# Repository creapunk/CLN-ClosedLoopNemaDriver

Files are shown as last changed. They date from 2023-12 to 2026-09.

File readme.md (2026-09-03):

# CLN - CLOSED-LOOP DRIVERS FOR NEMA MOTORS

    

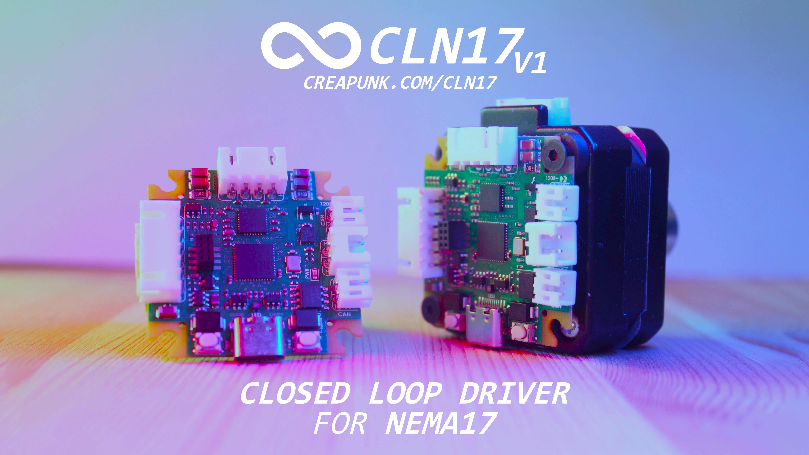
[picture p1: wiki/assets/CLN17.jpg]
CLN17 (https://www.youtube.com/watch?v=A67UROq0t6Q)


The CLN motor driver series is an **open-source** project aimed at creating a range of compact, cost-efficient high-performance closed-loop stepper drivers for various NEMA form factor motors. These drivers are designed to provide silent and smooth motion, high-precision position control, and energy-saving capabilities, suitable for a wide array of applications in robotics, CNC machines, 3D printers, and more.

## Key Features

- 🕹️ **Closed-Loop Control:** Integrates an encoder for real-time position monitoring, ensuring precise and safe motion.
- 📏 **Fine Positioning:** Achieves high position control accuracy of 0.01° for smooth operation.
- 🛡️ **Reliable Operation and Enhanced Safety:** Features integrated diagnostic and protection mechanisms for the motor and the user safety.
- 🧩 **Modular Concept:** Offers various configurations for different cost, size and performance needs, supporting expansion boards and daisy chain connections.

## Applications

- 🎓 Learning Platforms
- 🛠️ CNC Machines & 3D printers
- 🤖 Robotics & Automation Systems
- 🤝 Collaborative Robots
- 🔭 Camera & Telescope Stabilization Systems
- 🔬 Laboratory Equipment
- 🏭 Industrial Motion Control Systems
- 📳 Haptics & Force Feedback Systems

## Repository Structure

- **[`wiki`](wiki)**: includes design documentation and other information
- **[`hardware`](hardware)**: contains design source files, manufacturing files, schematics, block diagrams and 3D models

## Firmware

The following options are available:

- **[CLN-SimpleFOC](https://github.com/AntonEvmenenko/CLN-SimpleFOC):** SimpleFOC based firmware for CLN. Pretty stable, ready to use
- **[TunePulse](https://github.com/creapunk/TunePulse):** Firmware for CLN and RadiX motor drivers. Currently a work in progress; estimated release date is to be determined

## Hardware Versions

#### [NEMA17 dedicated drivers](./wiki/CLN17/readme.md)

- **[`CLN17 V3.0`](hardware/CLN17/V3.0)** [active]: newest version with best performance and BLDC support [[wiki]](./wiki/CLN17/V3.0/specification.md). 
  
  > - **Key info:** Discrete MOSFET based, 6-48V 3.2A<sub>RMS</sub> 4.5A<sub>PEAK</sub>, up to 60W output power, 21bit position feedback, dual-sided SMD only assembly
  > - **Supported interfaces:** STEP-DIR-EN, USB, CAN-FD, USART, I2C, SPI, ABZ
  > - **Supported motors:** Stepper, 3phase BLDC/PMSM
  >
  > 

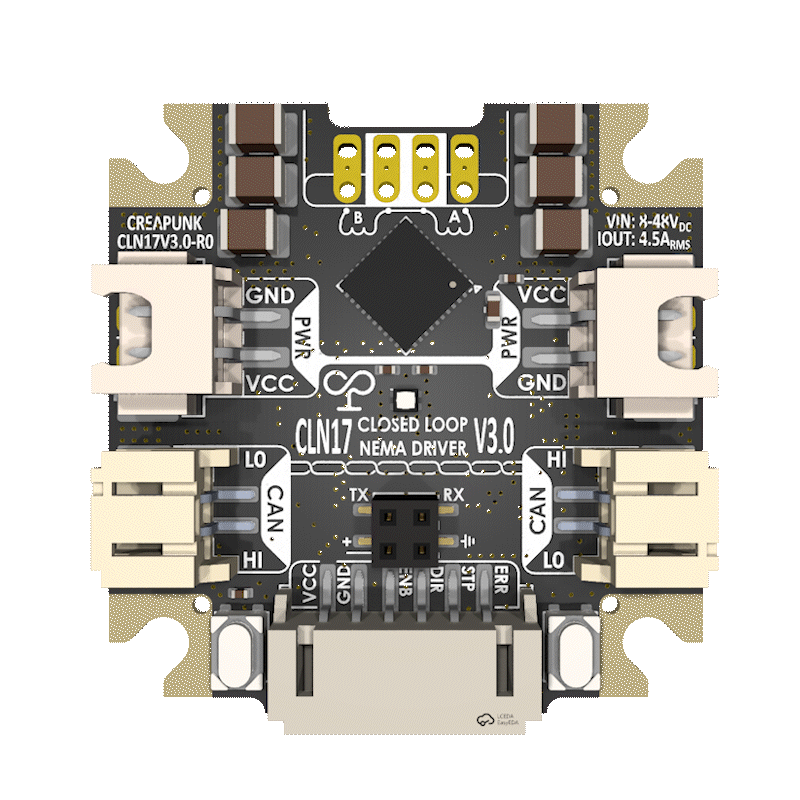
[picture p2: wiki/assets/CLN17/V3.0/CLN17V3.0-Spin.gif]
Preview
  

##### OBSOLETE / NRFND

**[`CLN17 V1.0`](hardware/CLN17/V1.0 [OBSOLETE])** [obsolete]: pilot version [[wiki]](./wiki/CLN17/V1.0/specification.md)

**[`CLN17 V1.5`](hardware/CLN17/V1.5 [OBSOLETE])** [tested]: cost-efficient version [[wiki]](./wiki/CLN17/V1.5/specification.md)

**[`CLN17 V2.0`](hardware/CLN17/V2.0 [NRFND])** [tested]: high voltage version [[wiki]](./wiki/CLN17/V2.0/specification.md). 
**[`CLN17 V2.1`](hardware/CLN17/ [NRFND])** is improved version

**[`CLN17 V2.5`](hardware/CLN17/V2.5 [NRFND])** [tested]: meant to be final version but will be skipped

***Important Note:** Obsolete designs will not be supported in future*

#### NEMA23 and NEMA34 dedicated drivers

- **[`CLN234 V1`](hardware/CLN234/V1.0)** [under tests]: powerful and versatile [[wiki]](./wiki/CLN234/V0.1/specification.md)

	> **Key info:** external MOSFETs, 8-75V 10A<sub>RMS</sub> 20A<sub>PEAK</sub>, up to 1000W output power, 21bit position feedback, 56x38x18mm, fits into Ø60mm
	>
	> **Supported interfaces:** STEP-DIR-EN, USB, CAN-FD, USART, I2C, SPI, ABZ
	
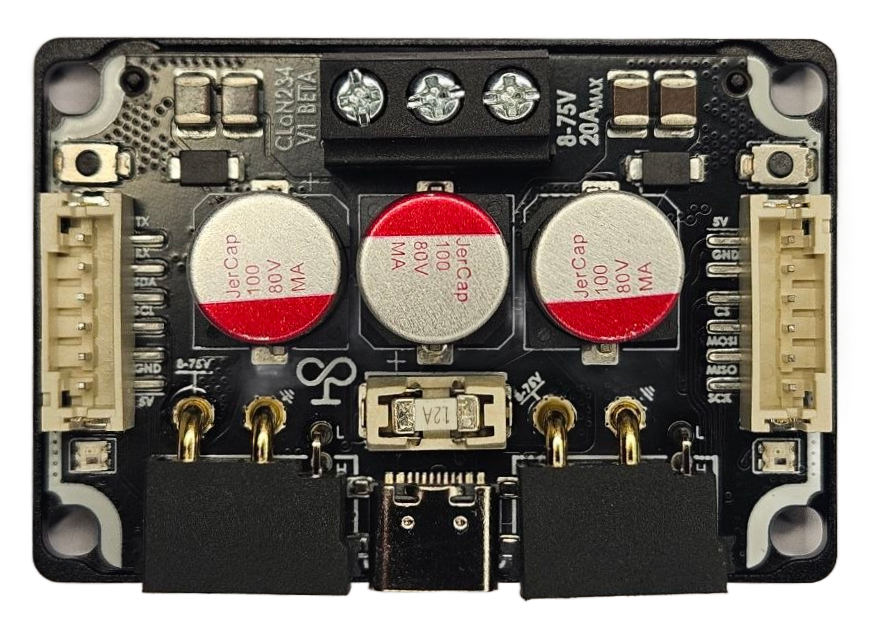
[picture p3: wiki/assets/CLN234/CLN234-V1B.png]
	

#### Modular drivers dedicated for embedded systems

Jump to the [RadiX project repository](https://github.com/creapunk/RadiX)

## Supporting the Project

If this project resonates with you, please consider the following ways to support its development:

- **[Ko-fi](https://ko-fi.com/creapunk):** Preferred for membership subscription and one-time donation
- **[Patreon](https://patreon.com/creapunk):** Alternative platform with higher fees
- **Join [Discord community](https://discord.gg/V4aJdTja8v):** Stay updated, engage in discussions, and contribute to the project

**Your contribution, regardless of size, is greatly appreciated!** 

*A heartfelt thank you to [everyone who supports this project](sponsors.md)!*

---

***Important Note:** This README will be updated to reflect the latest progress and changes in the project*.

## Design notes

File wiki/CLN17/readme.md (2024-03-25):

# CLN17 drivers series

| | CLN17 V2.0 | CLN17 V1.5 | CLN17 V1.0 |
| :---: | :---: | :---: | :---: |
| **MCU** | STM32G431CB<br/>M4 170MHz | STM32G431CB<br/>M4 170MHz | STM32G431CB<br/>M4 170MHz |
| **Memory** | 128KB FLASH<br/> 32KB SRAM | 128KB FLASH<br/> 32KB SRAM | 128KB FLASH<br/> 32KB SRAM |
| **Encoder** | TLE5012B<br/>15bit | TLE5012B<br/>15bit | TLE5012B<br/>15bit |
| **Driver** | DRV8844 | TMC2209 | TMC2209 |
| **Output power** | 8-48V<br/>1.75A<sub>RMS</sub> | 5-25V<br/>1.4A<sub>RMS</sub> | 5-25V<br/>1.4A<sub>RMS</sub> |
| **Max PWM frequency** | 75kHz | 40kHz | 40kHz |
| **Phase channel resistance** | 630mΩ | 270mΩ | 270mΩ |
| **Interfaces** | STEP-DIR<br/>USB2.0<br/>CAN-Bus FD<br/>USART<br/>I2C<br/>SPI / SSI<br/>ABZ | STEP-DIR<br/>USB2.0<br/>CAN-Bus FD<br/>USART<br/>I2C<br/>SPI / SSI<br/>ABZ | STEP-DIR<br/>USB2.0<br/>CAN-Bus FD<br/>UART<br/>I2C |
| **Size (WDH)** | 40x40x10mm | 40x40x10mm | 40x40x10mm |
| **Status** | Under testing | Tested | Obsolete |

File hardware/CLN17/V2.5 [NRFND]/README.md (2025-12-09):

- # CLN17 V2.5 Notes

	> #### Attention!
	>
	> This board has been tested, and the functionality of its main components has been confirmed. However, the board has several issues.
	>
	> You can proceed with its production, but it's recommended to wait for the updated V3 version. By using these files, you acknowledge and understand that:
	>
	> - This version is released for preview purposes only and may not receive future support.
	> - Any use of this version is at your own risk. The author is not responsible for any damage caused by the malfunction of this driver version.
	> - Subsequent versions may have changes in the BoM and the layout of all board components, including connectors.

	#### Known hardware issues:

	- Shorting VMOT when USB is plugged may cause unreversible damage of DCDC
	- Motor freewheeling when unpowered feature not work because of driver chip architecture
	- Current sensing may not work pr

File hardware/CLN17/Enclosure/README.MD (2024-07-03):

# Enclosure Design

> The enclosure design is compatible with all CLN17 drivers of versions V1.5, V2.0, [V2.5 future development].

### Stack

The enclosure consists of two halves: the **base plate**, which faces the motor, and the **cover**.

The **base plate** is responsible for positioning the board relative to the motor shaft and dissipating heat from the driver chip. The **cover** positions and secures the board within the **base plate** and protects the board from dust and mechanical damage.

A silicone thermal pad should be placed between the board and the **base plate**, specifically under the driver chip area.

The **cover** and **base plate** clamp the board between them using two DIN7991 M3x8mm screws located in two diametrically opposed threaded holes.

### Thermal Design

The most efficient heat dissipation from the driver chip is achieved through the copper and thermal vias in the board, rather than direct contact with the enclosure (due to R<sub>θJB</sub> Junction-to-board thermal resistance **<** R<sub>θJC(top)</sub> Junction-to-case thermal resistance).

Therefore, heat is conducted from the driver through PCB to the aluminum base plate via a silicone thermal pad.

The heat is then effectively distributed throughout the base plate due to its substantial thickness (2.5mm), reducing the temperature right under the driver chip.

Owing to the large thermal contact area between the base plate and the motor, the heat is evenly distributed between the motor and the base plate.

As a result, the driver can operate in an enhanced mode for an extended period without critical overheating, thanks to the motor's high thermal capacity.

Additionally, the built-in temperature sensor in the microcontroller allows for quick temperature readings (settling time <10s) of the aluminum plate (and consequently the motor), which further allows to optimize heat dissipation through algorithms.

### Enclosure Manufacturing

To manufacture the enclosure, two parts are required:

One `BASE-ALUMINUM.STEP` and one of [`COVER-POLYMER.STEP` or `COVER-POLYMER-TRANSPARENT.STEP` or `COVER-ALUMINUM.STEP`]. The choice is up to you.

Polymer parts can be made using any 3D printing process, though SLA is recommended.

For aluminum parts, the following requirements must be met to achieve best result:

- **Material:** Aluminum Alloys 6061, 5083, or 7075.
- **Minimum milling volume:** 45x45mm, with a thickness up to 10mm.
- **Milling Technology:** 3-axis milling on both sides.
- **Minimum tolerances and end mill diameter:** XY tolerance ±0.1mm, Z tolerance ±0.05mm, end mill diameter ≤ 2.0mm.
- **Postprocessing:** **Threading** of 2xM3 threads to a depth of 3mm, **chamfering**.
- **Surface finish:** Abrasive blasting, **anodizing** (preferably black).

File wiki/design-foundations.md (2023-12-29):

# Design Foundations

In any project, the philosophy and design concepts have a significant impact on its vision and purpose, extending beyond basic functionality. Incorporating design principles into the project can result in a solution that not only fulfills technical requirements but also resonates with users on an aesthetic level.

## Design philosophy

- 📖 **Open Source and Comprehensive Documentation:** Adopting an open-source philosophy invites wide-ranging engagement, making the project versatile and adaptable. Community involvement fosters innovation and knowledge exchange, creating a supportive ecosystem. Clear documentation promotes learning, collaboration, and seamless integration with other projects.
- 💎 **Aesthetic Appeal and Usability:** A technical product's aesthetic appeal should be a byproduct of its superior functionality, technological advancement, and usability.
- 💰 **Cost-Effectiveness and Accessibility:** Balancing cost and functionality while prioritizing accessibility ensures the project's seamless integration across various sectors.
- 🚀 **Future-Proofing:** Incorporating foresight for future improvements while maintaining the core design's integrity streamlines the development of new products. Proactively addressing and accommodating future requirements ensures the project's enduring viability and relevance.

## Design concepts

- 💪**High Performance:** The system should be capable of processing feedback data in real-time and react immediately by controlling the motor based on predefined algorithms. This simplifies the control process and reduces the load on the control device.
- 💻 **Compatibility and Versatility:** A wide range of supported interfaces should enable interaction with existing protocols as well as the implementation of new ones. This expands compatibility and facilitates integration of the device into existing systems.
- 🛡️ **Precision and Fault Tolerance:** The implementation of feedback control with position and current sensors should ensure precise positioning and mechanical load monitoring. This enables the detection and prevention of abnormal system operation when necessary.
- 🔧 **Adaptability:** Evaluating motor operating parameters and system displacement data enables the selection of an optimal motor control profile for the specified task.
- ⚡️ **Reliability and Power Efficiency:** Providing protection against electrostatic discharge (ESD), short circuits, and reverse polarity, as well as preventing overheating through reduced thermal losses, improved heat dissipation, and enhanced energy efficiency.
- 🧩 **Customizability and Modularity:** The device should accommodate functionality expansion or reduction without necessitating design changes.
- 🏭 **Optimized for Design for Manufacturing (DFM):** Complying with manufacturing technology requirements enhances manufacturability while reducing production costs and complexities.
- ⏳ **Longevity Considerations:** When choosing project component composition, future availability and support forecasts should be considered.

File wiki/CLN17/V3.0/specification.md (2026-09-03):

# CLN17-V3.0 Specification

## ⚡ Electrical characteristics

- **Input voltage:** 8-48VDC with overcurrent protection, reverse polarity protection and surge protection
- **Current requirements:** 3.2A<sub>RMS</sub> with up to 4.5A peak current
- **Powering options:**
	- 2-Pin connector **XH2.5** (3A limited by connector)
	- 6-Pin connector PH2.0 (2A limited by connector)
- **System voltage source:** 
	- On-board DC-DC converter
	- USB Type-C connector (5VDC 1.5A limited by design)

------

## 🔄 Motor Driving Control Capabilities

- **Best stepper motor form factor:** NEMA17
- **Maximum coil current:**
	- **3.0A<sub>RMS</sub>** per phase continuously
	- **4.5A<sub>PEAK</sub>** per phase continuously with heatsink
- **Maximum output voltage:** 48VDC
- **Maximum step sub-division resolution:** 1/256 of full step
- **Energy saving features:** Passive Braking, Freewheeling and automatic power down
- **Working frequency:** up to 83kHz PWM
- **Phase channel resistance:** MOSFETs RDS<sub>ON</sub> 45mΩ for both sides + 15mΩ current sensing resistor
- **True Driver positioning resolution:** Up to 0.028° (may be limited by motor)
- **True Encoder position feedback resolution:** 21bit per full rotation
- **Diagnostic functions:** overheat detection, short-circuit detection, under-voltage detection, open-load detection in case connectors are not firmly plugged in

------

## 🖥️ MCU Performance and External interfaces

**MCU:** High-performance Arm Cortex-M4 MCU **STM32G431CB** running at **170MHz** with:

* **128KB Flash** memory and **32KB SRAM** memory and **1Kb OTP**
* Math accelerator with trigonometric functions calculations support;
* True random number generator
* Internal HSI and RTC with external oscillator option

**Interfaces:**

* **USB2.0** for PC communication
* **CAN-Bus** with CAN-FD support for high-speed or long-range wired connection with daisy chain connection option

- **SWD** programming interface with debug over SWO trace
- **6-Pin CTRL connector PH2.0** with multifunctional bidirectional fast 4-Pin interface up to 8MHz with support:
  * **Classic EN/DIR/STEP** interface with **ERR line**

  * **USART** (Single wire, Asynchronous, Synchronous)

  * **I2C**

  * **SPI or SSI**

  * **ABZ incremental interface** for external encoder connection with program-controlled **5V voltage source**

  * **Custom interface** including numerous combination of the above interfaces
- **4-Pin expansion connector 2x2P2.0** with 2A power line and multifunctional bidirectional fast 2-Pin interface up to 8MHz with **Classic UART** interface

**I/O protection features**:

* ESD protection (persistent against electrostatic discharge)
* USB, SWD and control interfaces are 5V-tollerant
* Reverse polarity signal protection
* Overcurrent protection

**User interaction:**

*  **2** programmable custom **user buttons** (one can be used as reset button)
*  **RGB LED** for indication of working mode or current status

------

## 📏 Mechanical data

- **Size dimensions:** PCB outline is 40x40mm (adapted for NEMA17 form factor) 8.5-13mm total height (depends on the connectors type)
- **Driver housing:** 42x42mm CNC-milled alluminum case for PCB mounting, heatsink and mechanical protection with
- Weight: 
	- **10g**   board only
	- **20g** board with mount

------

## 🔥 Operating conditions

* **Working temperature range:** **-25 to +80** degrees Celsius
* **Environment humidity range:** 0 to 90%
* **Environmental safety:** potential **Lead-Free** and **RoHS** compliance
* **Maximum heat dissipation**: 3W from motor driver and 0.5W from other system

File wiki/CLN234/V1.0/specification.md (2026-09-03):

# CLN234-V1 Specification

## ⚡ Electrical characteristics

- **Input voltage:** 8-75VDC with overcurrent protection, reverse polarity protection and surge protection
- **Current requirements:** 10A<sub>RMS</sub> with up to 20A peak current
- **Powering options:**
	- XT30 2+2
- **System voltage source:** 
	- On-board DC-DC converter
	- USB Type-C connector (5VDC 1.5A limited by design)

------

## 🔄 Motor Driving Control Capabilities

- **Supported motor type:** Dual DC, Steppers, BLDC, PMSM
- **Supported NEMA motors:** NEMA23, NEM34, NEMA42, other
- **Maximum phase current:**
	- **10A<sub>RMS</sub>** per phase continuously
	- **13A<sub>RMS</sub>** per phase with 50% duty cycle (period 1s)
	- **20A** peak per phase
- **Maximum output voltage:** 75VDC
- **Maximum step sub-division resolution:** 1/512 of full step
- **Energy saving features:** Passive Braking, Freewheeling and automatic power down
- **Working frequency:** up to 83kHz PWM
- **Phase channel resistance:** Mosfets RDS<sub>ON</sub> 20mΩ for both sides + 2.5mΩ current sensing resistor
- **Encoder position feedback resolution:** 21bit per full rotation
- **Diagnostic functions:** overheat detection, short-circuit detection, under-voltage detection, open-load detection

------

## 🖥️ MCU Performance and External interfaces

**MCU:** High-performance Arm Cortex-M4 MCU **STM32G431CB** running at **170MHz** with:

* **128KB Flash** memory and **32KB SRAM** memory and **1Kb OTP**
* Math accelerator with trigonometric functions calculations support;
* True random number generator
* Internal HSI and RTC with external oscillator option

**Interfaces:**

* **USB2.0** for PC communication
* **CAN-Bus** with CAN-FD support for high-speed or long-range wired connection with daisy chain connection option

- **SWD** programming interface with debug over SWO trace
- First **5-Pin CTRL connector PH2.0**:
  * **Classic EN/DIR/STEP** interface with **ERR line**
  * **USART** (Single wire, Asynchronous, Synchronous)
  * **SPI or SSI**
  * **ABZ incremental interface** for external encoder connection with program-controlled **5V voltage source**
- Second **5-Pin CTRL connector PH2.0**:
	- **Classic EN/DIR/STEP** interface or **DIR/STEP** with **ERR line**
	- **I2C**
	- **ABZ incremental interface** for external encoder connection

- **4-Pin expansion connector 2x2P2.0** with 2A power line and multifunctional bidirectional fast 2-Pin interface up to 8MHz with **Classic UART** interface

**I/O protection features**:

* ESD protection (persistent against electrostatic discharge)
* USB, SWD and control interfaces are 5V-tollerant
* Reverse polarity signal protection
* Overcurrent protection

**User interaction:**

*  Reset button

------

## 📏 Mechanical data

- **Size dimensions:** 
	- PCB outline: 54x54mm (adapted for NEMA23 form factor)
	- PCB circumcircle radius: 60mm
	- PCBA Height: 15mm

- Weight: 
  - **8g**   board only
  - **18g** board with mount
  - **24g** with **low-profile** aluminum housing
  - **28g** with **full-size** aluminum housing

------

## 🔥 Operating conditions

* **Working temperature range:** **-25 to +80** degrees Celsius
* **Environment humidity range:** 0 to 90%
* **Environmental safety:** potential **Lead-Free** and **RoHS** compliance
* **Maximum heat dissipation**: 20W from motor driver and 0.5W from other system

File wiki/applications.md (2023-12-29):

# Applications

The CLN17 Stepper Motor Driver is suitable for a wide range of applications, including but not limited to the listed below.

## Learning and Research

- 🎓 **Learning Platforms:** Open-source designs and clear documentation provide universal motor control learning solutions, promoting innovation and collaboration among students and educators. <br/>*Examples: Robotic arm kits; Solar tracking systems.*
- 🔬 **Laboratory Equipment:** Precision, safety, and feedback features are crucial for reliable operation, accurate results and researcher safety. <br/>*Examples: Automated liquid handling systems; Precision sample positioning systems.*
- 🤝 **Cobots and Learning Systems:** Accurate shaft position and speed detection make the motor driver suitable for cobots and learning systems, enabling safe human-machine collaboration. <br/>*Examples: Humanoid robots for social interaction; Collaborative robotic arms for assembly tasks.*

## Robots and Automotion

- 🛠️ **CNC Machines & 3D Printers:** Precision and error-free positioning are essential for accurate manufacturing in CNC machines and 3D printers. <br/>*Examples: High-speed or large-format 3D printers; Laser cutting and engraving machines; Desktop CNC milling machines.*
- 🤖 **Robotics & Automation Systems:** Precise control and movement enhance overall performance in robotics and automation. <br/>*Examples: Autonomous mobile robots; Pick-and-place robotic systems.*
- 🏭 **Industrial Motion Control Systems:** Reliability and compatibility with industrial interfaces improve performance in industrial motion control.<br/>*Examples: Conveyor systems and Delta-Robots; Automated assembly lines.*

## Haptic and Stabilization

- 📳 **Haptics & Force Feedback Systems:** Accurate current and force control are vital for realistic haptic and force feedback experiences. <br/>*Examples: Teleoperation systems for remote control; Virtual reality controllers with force feedback.*
- 🔭 **Camera/Telescope Stabilization Systems:** Stable orientation in camera and telescope systems relies on precise positioning and position holding, simplifying system calibration for accurate component alignment. <br/>*Examples: Motorized telescope mounts; Video camera sliders.*

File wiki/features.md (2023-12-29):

# Features

## Position Control and Accuracy

- 🕹️ **Closed-Loop Control:** The motor driver supports closed-loop control, integrating an encoder for real-time position monitoring and adjustment, ensuring precise motion in challenging conditions.
- 📏 **Fine Positioning:** Exceptional position control accuracy of 0.01° ensures efficient and low latency processing of position information and minimal noise for smooth operation.
- 🎯 **Extremely Precise and Repeatable Sensorless Parking:** The sophisticated sensorless parking algorithm accurately positions the motor without additional sensors, preventing system damage.

## Performance and Efficiency

- 💪 **Adaptive Torque Control and Energy Efficiency:** The motor driver adjusts torque based on load requirements, optimizing energy efficiency, reducing stress, and extending motor lifespan.
- 🚀 **High Performance:** A 32-bit 170MHz ARM Cortex®-M4 microprocessor delivers significant performance improvements and ample power for application code.
- 🔇**Ultra-Silent and Smooth Operation:** The silent motor driver guarantees quiet and smooth operation for noise and vibration-sensitive applications.
- ⏩ **Passive braking and freewheeling:** Smooth deceleration and coasting of the motor are enabled by passive braking and freewheeling functionalities, enhancing control and efficiency.

## Compatibility and Modularity

- 🤝 **Open-Source Approach:** Complete access to hardware schematics, PCB layouts, firmware, and software fosters transparency, collaboration, and innovation, enabling the creation of customized solutions.
- 💻 **Enhanced compatibility:** Versatile connectivity options, including UART, I2C, CAN-Bus (with FD support), USB2.0 over Type-C and more, facilitate seamless communication and easy integration into existing systems.
- 🧩 **Modular Concept:** Various configurations meet size and performance requirements while maintaining cost-effectiveness, supporting expansion boards for additional functionalities.
- 🌐 **Efficient Daisy Chain Interconnection:** Enables direct connection of multiple drivers, simplifying setup and reducing the need for extra interfacing hardware.

## Safety and Reliability

- 🔧 **Robust and Reliable Performance:** Designed to operate reliably across a wide temperature range. Includes diagnostic functions and built-in protections against ESD, current limitation, reverse polarity, overload, and supports 3.3V/5V IO tolerance.
- 🛡️ **Intelligent Safety Algorithms:** Advanced algorithms continuously monitor motor conditions, providing proactive protection to both the motor system and users from potential harm.
- ⏰ **High-Precision Real-Time Clock:** Incorporates a precise clock source, essential for time-sensitive operations, ensuring accurate timing for critical tasks and reliable code execution.

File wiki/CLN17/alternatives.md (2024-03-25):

# Alternative Closed-Loop Drivers for NEMA17

CLN17 is not the only closed-loop motor driver. There are several alternatives available, which are also closed-loop drivers and designed with a similar architecture. These drivers comprise a microcontroller, an encoder, and a driver, all integrated onto a single printed circuit board placed at the rear side of the NEMA17 motor.

## Quick overview of the alternatives

- [USTEPPER S32](https://github.com/uStepper/uStepperS) by [uStepper](https://github.com/uStepper)
- [MKS SERVO42C](https://github.com/makerbase-mks/MKS-SERVO42C) by [Makerbase](https://github.com/makerbase-mks)
- [MECHADUINO](https://github.com/jcchurch13/Mechaduino-Hardware) by [jcchurch13](https://github.com/jcchurch13)
- [XDrive](https://github.com/unlir/XDrive) by [unlir](https://github.com/unlir)
- [BTT S42C](https://biqu.equipment/products/bigtreetech-s42c-v1-0-42-stepper-motor-closed-loop-driver-board-with-oled-display) by [BigTreeTech](https://github.com/bigtreetech)
- [Smart Stepper](https://github.com/Misfittech/nano_stepper) by [Misfittech](https://github.com/Misfittech)
- [Ethersweep](https://github.com/Neumi/ethersweep) by [Neumi](https://github.com/Neumi)

| | CLN17 V2 | USTEPPER S32 | MKS SERVO42C | BTT S42C | MECHADUINO | Smart Stepper | XDrive | Ethersweep |
| :---: | :---: | :---: | :---: | :---: | :---: | :---: | :---: | :---: |
| **MCU** | STM32G431CB<br/>M4 170MHz | STM32F401RE<br/>M4 84MHz | HC32L130F8<br/>M0 48MHz | STM32G031G8<br/>M0+ 64MHz | ATSAMD21G18<br/>M0+ 48MHz | STM32F103CB<br/>M3 72MHz | STM32F103CB<br/>M3 72MHz | STM32F103C8<br/>M3 72MHz |
| **Memory** | 128KB FLASH<br/> 32KB SRAM | 512K FLASH<br/>96K SRAM | 64KB FLASH<br/>8KB SRAM |  64KB FLASH<br/>8KB SRAM  | 256KB FLASH<br/>32KB SRAM | 256KB FLASH<br/>32KB SRAM | 128KB FLASH<br/>20KB SRAM | 64KB FLASH<br/>20KB SRAM |
| **Encoder** | TLE5012B<br/>15bit | TLE5012B<br/>15bit | MT6816<br/>14bit | TLE5012B<br/>15bit | AS5047D<br/>14bit | AS5047D<br/>14bit | MT6816<br/>14bit | AS5600<br/>12bit |
| **Driver** | DRV8844 | TMC5130 | EG3013<br/>CJ3400 | EG3013<br/>A03400 | A4954 | A4954 | TB67H450 | TMC2209 |
| **Output power** | 8-48V<br/>1.75A<sub>RMS</sub> | 8-42V<br/>1.4A<sub>RMS</sub> | 7-28V<br/>3.0A<sub>RMS</sub> | 12-24V<br/>3.0A<sub>RMS</sub> | 8-25V<br/>2.0A<sub>RMS</sub> | 8-35V<br/>2.0A<sub>RMS</sub> | 6-38V<br/>2.5A<sub>RMS</sub> | 6-30V<br/>1.4A<sub>RMS</sub> |
|  **Interfaces**  | STEP-DIR<br/>USB2.0<br/>CAN-Bus FD<br/>USART<br/>I2C<br/>SPI / SSI<br/>ABZ | STEP-DIR<br/>UART<br/>SPI<br/>I2C | STEP-DIR<br/>UART | STEP-DIR<br/>UART<br/>SPI | STEP-DIR<br/>USB2.0<br/>SPI<br/>I2C | STEP-DIR<br/>USB2.0<br/>UART<br/>I2C | STEP-DIR<br/>USB2.0 or CAN-Bus<br/>RS485 | USB2.0<br/>SPI<br/>I2C<br/>Ethernet |
|  **Size (WDH)**  | 40x40x10mm | 42x42x12mm | 43x40x12mm | 40x40x12mm | 42x42x16mm | 42x42x16mm | 40x40x12mm | 40x40x25mm |
| **Status** | Open-Source | Open-Source | Open-Source | Proprietary | Open-Source | Open-Source | Open-Source | Open-Source |

> The following information is sourced from the analysis of datasheets, official descriptions, and other reliable sources. However, please note that it may be outdated, inaccurate, or incomplete.

## Is there anything else?

There are several other similar products available, but they haven't been described due to the project's confidentiality or lack of information.

- [Emm42](https://github.com/Macrobase-tech/Emm42) by [Macrobase-tech](https://github.com/Macrobase-tech). Status: proprietary
- [AnanasStepper](https://github.com/AnanasRobot/AnanasStepper) by [AnanasRobot](https://github.com/AnanasRobot). Status: V3.0 not released
- [PANdrive](https://www.trinamic.com/products/pandrive-smart-motors/) by [Trinamic](https://www.trinamic.com/). Status: proprietary

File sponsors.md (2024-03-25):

# Project Contributors
A Heartfelt Thanks to Project Supporters and Contributors!

### Industry Supporters

Special thanks to [JLCPCB](https://jlcpcb.com/?from=creapunk) for their support with board manufacturing!

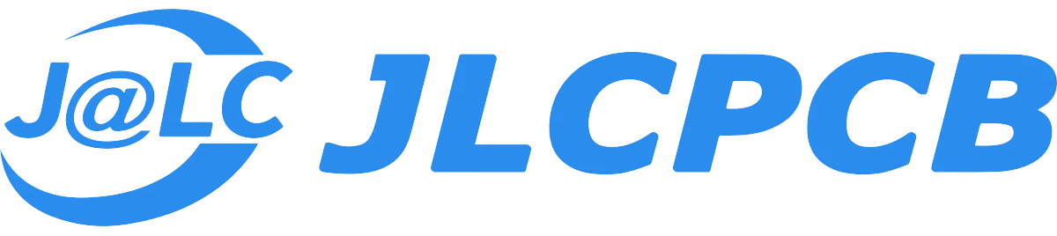
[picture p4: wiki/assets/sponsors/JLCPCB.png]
(https://jlcpcb.com/?from=creapunk)


## Community Sponsors

I'm grateful for the contributions from our community sponsors:

- Miral Patel

- @keverin16

- @olov

- @sharwin24

- @Denis2020

- @raghava

- @nathanjaker

- Henry Well

- Jeremy Fleming

- Robert Montini

- Vincent Wüthrich

Your support makes a significant difference in our project's progress. Thank you!

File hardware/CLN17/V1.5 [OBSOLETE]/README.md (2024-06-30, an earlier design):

#  CLN17 V1.5 HARDWARE



Compact driver for NEMA17, a corrected and improved version of CLN17 V1.0, suitable for 12V and 24V systems with a current of up to 1.4A RMS.

`STATUS` As of January 2024, the [board's functionality has been confirmed](#tested-hardware-features), with no problems identified. Firmware is in progress.

- [`Specification`](/wiki/CLN17/V1.5/specification.md)
- [`PCBA Manufacturing`](#pcba-manufacturing-specification)

------

### Board Diagram

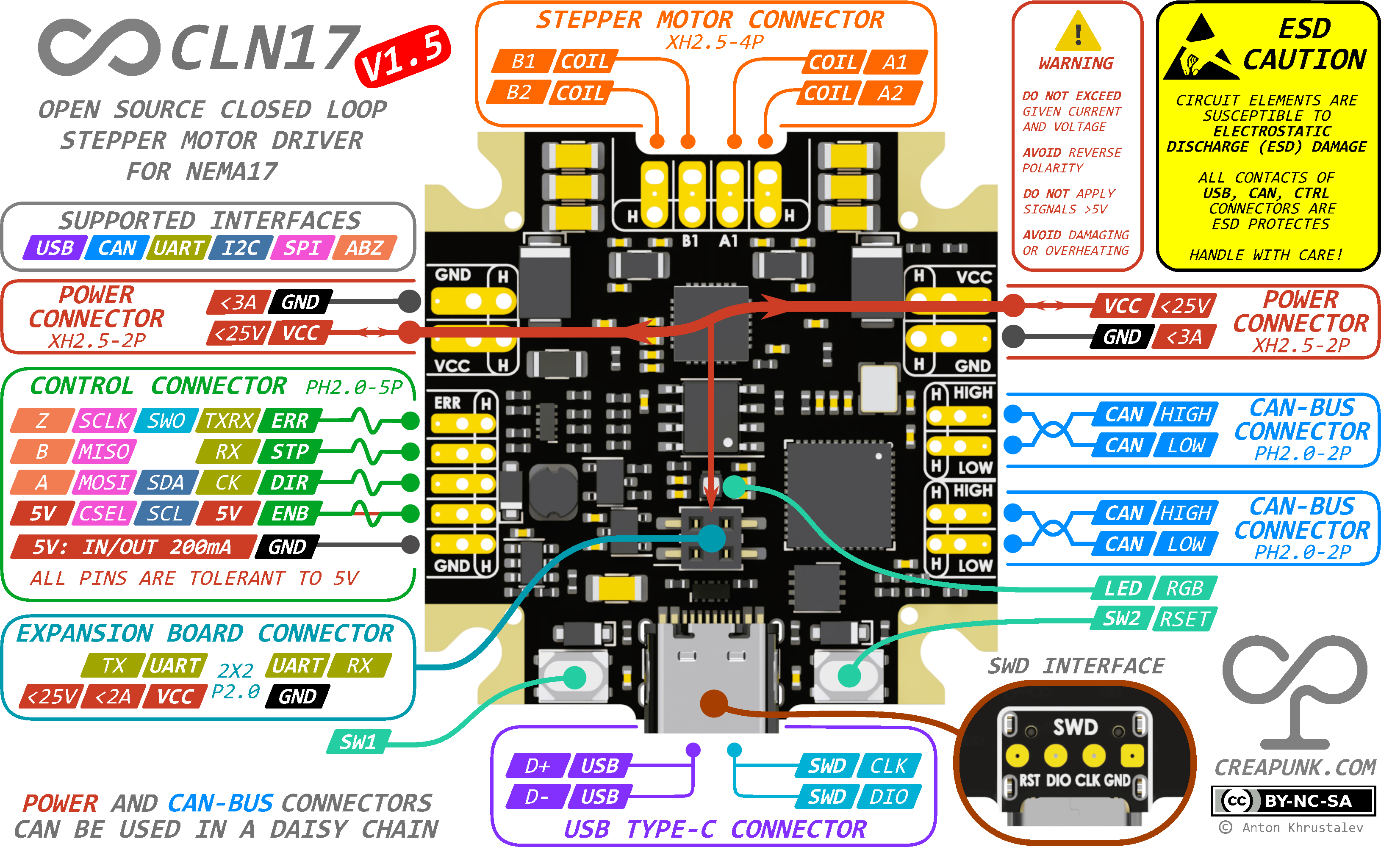
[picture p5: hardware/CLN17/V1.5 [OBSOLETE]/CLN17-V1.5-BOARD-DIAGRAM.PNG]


------

### Attention!

> - **Uncompleted firmware:** Firmware of CLN17 V1.5 driver is in active development. May contain unforeseen issues.
>
> - **Potential Design Changes:** The design may undergo minor modifications in the future.
>
> - **No Author Liability:** The author bears no responsibility for any damages resulting from incorrect usage, connections, manufacturing faults, or coding errors.
>
> - **User's Duty:** Users must conduct comprehensive tests in their specific environments. Adherence to provided usage guidelines is crucial.

------

### Tested hardware features

Driver IC:

- ✅ TMC2209 STEP-DIR, UART SW bidirectional communication, Reset + Disable functionality
- ✅ Freewheeling when unpowered
- ✅ Analog Current sensing

Encoder IC:

- ✅ TLE5012 SPI communication
- ✅ TLE5012 through the PCB position sensing (1LSB noise)

Power:

- ✅ Daisy Chain Power connection
- ✅ DCDC stability at voltage range [External: 5.2V-25V, USB: 4.9V-5.5V]
- ✅ ENB CLTR 5V (Power Sink & Source 5V 200mA)

Interfaces:

- ✅ USB communication
- ✅ CTRL connector - UART, I2C, SPI communication (ABZ not tested yet)
- ✅ CAN-Bus IC Shutdown and Logic supply, diff signal generation
- ✅ Expansion connector - UART communication
- ✅ SWD with reset functionality

Peripherals:

- ✅ SW1 & SW2 as button
- ✅ RESET using SW2 as output
- ✅ RGB LED (single color indication)
- ✅ External Precise Clock (10ppm) (HSE)

------

### PCBA Manufacturing Specification

- **Layers**: 4
- **Minimum Via Hole Size/Via Diameter**: 0.25mm/0.41mm
- **Minimum track width/spacing**: 0.13mm/0.13mm
- **Material**: FR4
- **PCB Thickness**: 1mm [preferred]
- **PCB Color**: Any, but black is more aesthetic.
- **PCB Surface Finish**: ENIG [preferred]
- **Outer/Inner Copper Weight**: 1oz/0.5oz
- **Via Covering**: Plugged [preferred] or Tented
- **Board Outline Tolerance**: ±0.2mm
- **Panelization**: optional, but if horizontal connectors used, the gap between boards should be ≥5mm.
- **Assembly**: Single top side
- **Tooling Holes**: Already present 4x D1.152mm in the corners of the board. May require modification for specific equipment.

#### Important Notes

> ***Non-stock Components Note:** The design features 3 irreplaceable components: the driver chip, microcontroller, and encoder. Other parts can be replaced with in-stock equivalents that match or surpass the original specs, provided you conduct a schematic review beforehand.*

> ***Cost Reduction Note:** Eliminate unused components such as the CAN-Bus or CTRL connector to reduce costs, provided you conduct a schematic review beforehand.*

------

### Support the Project!

**If you like the project and want to support its development, you can do so through:**

- **[Ko-fi](https://ko-fi.com/creapunk)** (*preferred for membership subscription and one-time donation*) - here, you can sign up for monthly support, or you can make a one-time donation as well!
- **[Patreon](http://patreon.com/creapunk)** - similar to Ko-fi, but with higher fees.

Don't forget to join **[creapunk community on Discord](https://discord.gg/4uFSsffhMt)** for the latest updates and discussions!

------

Special thanks to [JLCPCB](https://jlcpcb.com/?from=creapunk) for sponsoring the board manufacturing of this design!

(https://jlcpcb.com/?from=creapunk)

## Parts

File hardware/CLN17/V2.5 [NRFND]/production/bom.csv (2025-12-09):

Designator | Footprint | Quantity | Value | LCSC Part #
C1, C12, C13, C14, C5, C8, C9 | C1210 | 7 | 10u 100V | C5156756
C10 | C0402 | 1 | 2.2u | C12530
C11, C15, C29 | C0402 | 3 | 1u | C52923
C16, C2, C20, C35 | C0402 | 4 | 10u | C15525
C17, C18, C21, C22, C25, C26, C28, C3, C31, C4 | C0402 | 10 | 100n | C1525
C23 | C0603 | 1 | 22n 100V | C313083
C6, C7 | C0402 | 2 | 12p | C1547
D1 | D_SMAF | 1 | SMBJ48A | C353356
D3, D7 | D_SOD-123F | 2 | SS210 | C183475
D4 | D_SMAF | 1 | ES3BF | C437835
D6 | LED_RGB_0606 | 1 | LED_RABG | C2874115
FB1 | R0402 | 1 | <1R | C76883
IC1 | QFN-48-1EP_7x7mm_P0.5mm_EP5.6x5.6mm | 1 | STM32G431CB | C529356
J1, J2 | XH2.54 2P | 2 | PWR | C2908611
J3 | USB-TYPE-C-31-M-12 | 1 | TYPE-C-31-M-12 | C2988369
J4 | XH2.54 4P | 1 | Motor | C5188444
J5 | PH2.0 5P | 1 | CTRL | C2908637
J6, J7 | PH2.0 2P | 2 | CAN | C2908634
J9 | 2x2P2.00mm_Vertical_SMD | 1 | IO | C2911301
L1 | CD32 | 1 | 33u 600mA | C492262
Q1 | SOT-23-3 | 1 | AO3401 | C15127
R1, R17, R18, R19, R2, R23, R26, R3, R35, R4 | R0402 | 10 | 120 | C25079
R10, R14, R20, R21, R22, R27, R29, R37, R8 | R0402 | 9 | 5.1k | C25941
R11, R12, R24, R25 | R0402 | 4 | 2.7k | C25885
R13 | R0402 | 1 | 100k | C25741
R15, R33, R36 | R0402 | 3 | 510 | C25123
R16, R5 | R0402 | 2 | 150k | C25741
R32, R6 | R0402 | 2 | 10k | C25744
R7 | R0402 | 1 | 330k | C25778
R9 | R0402 | 1 | 27k | C25771
SW1, SW2 | SW_SPST_PTS810 | 2 | SW_Push | C2888430
U10, U5 | DFN-2510 | 2 | H5VU25U | C7420374
U12 | max22208 | 1 | MAX22208 | C22471610
U2 | SOIC-8_3.9x4.9mm_P1.27mm | 1 | TLE5012B | C123083
U3 | MSOP-TSSOP-8-P0.65mm | 1 | AT24CS01-XHM | C2832785
U4 | SOT-23-3 | 1 | ME6211 | C168807
U8 | HVSON-8-1EP_3x3mm_P0.65mm_EP1.6x2.4mm | 1 | TJA1042 | C131480
U9 | SOT-23-6 | 1 | BL9362 | C2909086
Y1 | Oscillator_SMD_Kyocera_KC2520Z-4Pin_2.5x2.0mm | 1 | 12M | C9002

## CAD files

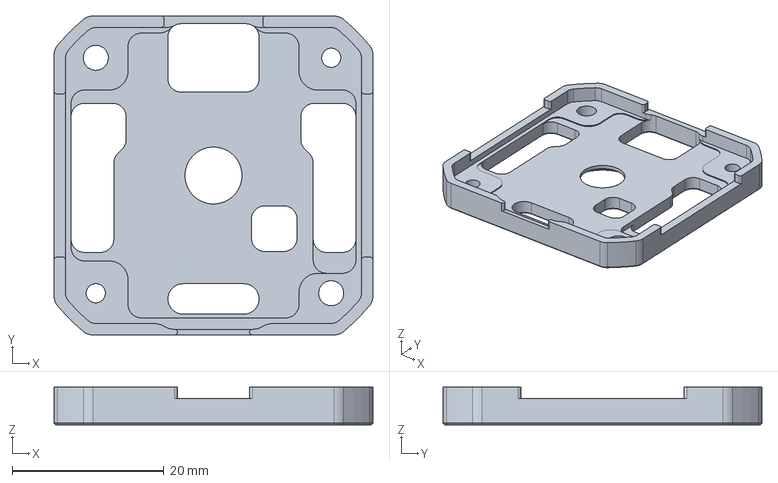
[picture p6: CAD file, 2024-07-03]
hardware/CLN17/Enclosure/BASE-ALUMINUM.STEP
42.0 x 42.0 x 5.00 mm

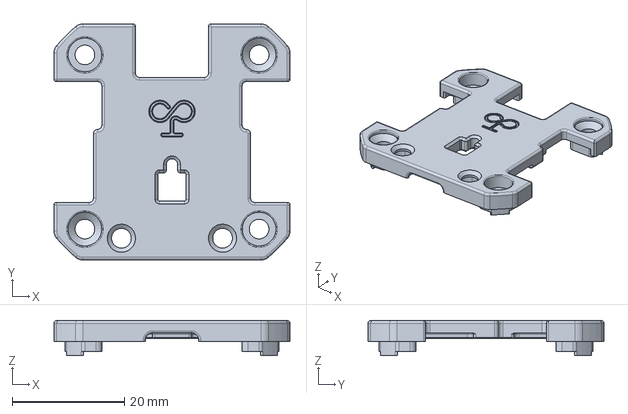
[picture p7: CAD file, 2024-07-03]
hardware/CLN17/Enclosure/COVER-POLYMER.STEP
42.0 x 42.0 x 6.25 mm

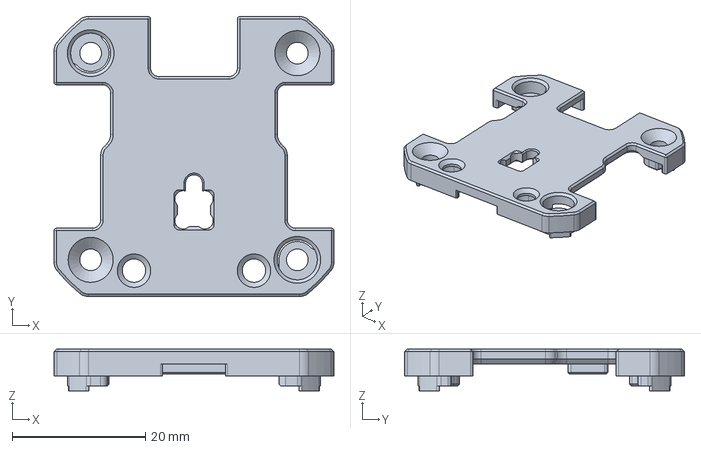
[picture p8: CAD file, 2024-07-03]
hardware/CLN17/Enclosure/COVER-ALUMINUM.STEP
42.0 x 42.0 x 6.25 mm

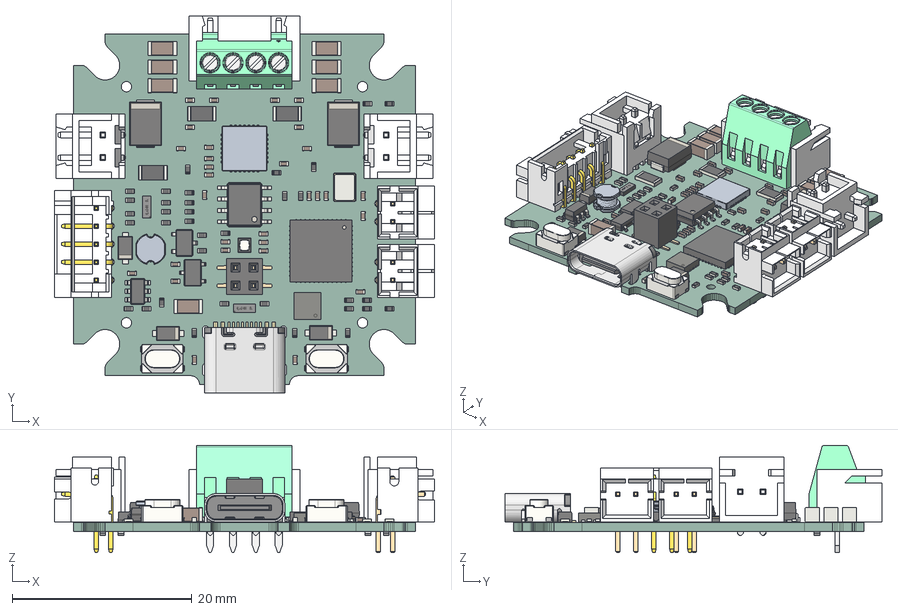
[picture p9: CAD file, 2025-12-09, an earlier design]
hardware/CLN17/V1.5 [OBSOLETE]/CLN17-V1.5-3D.STEP
42.2 x 41.9 x 11.9 mm
CLN17-V1.5 PCB

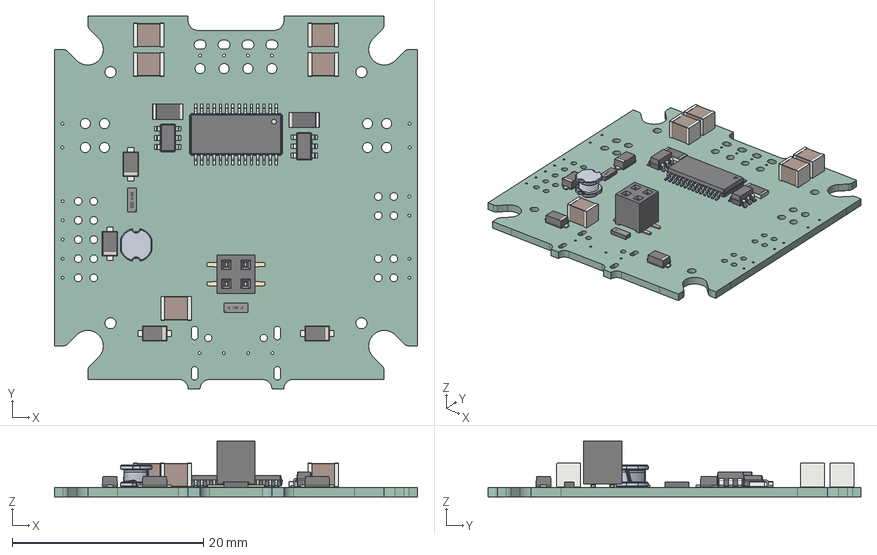
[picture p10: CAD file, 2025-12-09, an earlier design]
hardware/CLN17/V2.0 [NRFND]/CLN17-V2.0-3D.STEP
38.0 x 39.0 x 5.85 mm
D_SOD_123F x 4
R_1206_3216Metric x 2
C_1210_3225Metric x 5
DFN2510-10L x 2
PinSocket_2x02_P200mm_Vertical_SMD
HTSSOP_28_1EP_44x97mm_P065mm
SOT_23_6 x 2
_autosave-CLN17-V2.0_PCB

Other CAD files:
hardware/CLN17/Enclosure/COVER-POLYMER-TRANSPARENT.STEP

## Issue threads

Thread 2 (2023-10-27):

FR: For the Advanced Version

Oakman-Dev, 2023-10-27:
I saw that you're working on an advanced version with a TMC5160 driver, for this version I'd recommend looking into the Broadcom AEAT-9955 encoder, I've had great experiences with it and it also supports 18-bit resolution / 20000CPR. They also have a AR25-AB series that's supposed to go to 25-bit as well, but haven't tested that.

Oakman-Dev, 2023-11-02:
That's really cool, I haven't seen the MT6835 it seems like a great choice! Looking forward to trying the advanced version.

dzid26, 2023-11-16:
- What's wrong with TLE5012b ?  Too noisy for you? @FutureEngineeer
- What is a application of higher resolution? 15bit already gives 0.01deg @Oakman-Dev

@FutureEngineeer you should transfer those issues to Discussion section ;)

FutureEngineeer, 2023-11-16:
@dzid26

For NEMA17 the TLE5012 is a great option for the price and is exactly what I use.

However, larger motors may require more accuracy. For example, there are 50k+ PPR eneoders, which are used for example in P&P machines. So for larger motors it makes sense to use a more advanced encoder.

Also MT6835 seems to have an internal calibration capability without having to store all data in the MCU memory

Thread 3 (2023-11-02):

Similar design for nema 23 and nema 34 wanted.

hemangjoshi37a, 2023-11-02:
Can you please design anything similar for  nema 23 and nema 34 ?

FutureEngineeer, 2023-11-02:
Already in progress)

hemangjoshi37a, 2023-11-03:
@FutureEngineeer  Thank you sir. Please let me know if you  need any help. I can collaborate on this.

Badwolf101, 2023-11-04:
I'm really interested in the project to use it on nema 14, I think the challenge is to design it for smaller motors, then just enlarge the size of the pcb

ardlc-1212, 2023-11-10:
> I'm really interested in the project to use it on nema 14, I think the challenge is to design it for smaller motors, then just enlarge the size of the pcb

Not exactly... He would have to accomodate for bigger mosfets needed for the larger motors. Additionally there is hysteresis differences etc. that would require some additional testing

thijstriemstra, 2023-11-12:
I'd also be very interested in a nema23 version for a clay extruder I'm building.

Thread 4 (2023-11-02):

Can you please  design this using esp32 as microcontroller instead STM one ?

hemangjoshi37a, 2023-11-02:
Can you please design this using esp32 as microcontroller instead STM one ?
https://hjlabs.in/

FutureEngineeer, 2023-11-02:
Nope, ESP32 is a much poorer choice as a driver controller. However, if you need BLE/Bluetooth/WiFi then you can make an expansion board. I might do it myself if there is a demand for it

DRCBR1, 2023-11-02:
yes please, we would appreciate it 🙏🏼
(or any other suggestion (than esp32) to add WiFi)

hemangjoshi37a, 2023-11-03:
@FutureEngineeer The main problem with STM microcontroller is that is very hard to get in Bharat and even purchasing it from out of Bharat is very costly. Also it lacks WiFi and Bluetooth. I dont understand how is it wrong choice for driver controller. If you can explain what is wrong with esp32 that is done correctly with STM microcontroller.

FutureEngineeer, 2023-11-03:
STM32G431 costs only $1.7, but it is much faster than ESP32 (about 3 times faster in a comprehensive test). Additionally, STM32 has much more peripherals, it is much more convenient to work with timers, less components are required, much better built-in ADC, much better pin timings. Additionally there are hardware CAN-FD, CORDIC and FPU.

Collectively, among ESP32/RP2040/STM32G4 microcontrollers, the latter is much better. This microcontroller is available for purchase both through ST.com and through intermediaries like LCSC and others.

If you need a design without STM32 but only with SP32, you can make it yourself)

Closed 2023-11-12.

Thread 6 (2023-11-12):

GND and VCC markers are reversed？

CodeMan-P, 2023-11-12:
The GND and VCC markings on the right side of the top layer are reversed

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

FutureEngineeer, 2023-11-12:
@CodeMan-P Indeed. Thanks for noticing) I'll fix it in the documentation for the newer version)

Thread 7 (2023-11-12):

About PB8-BOOT0

ShenYuan-sean, 2023-11-12:
Hello, It seems that you used pb8, which is the boot0 pin, as the CAN_RX function. How does it make sense? Because boot0 needs to be connected to GND for the MCU start-up for internal flash. Looking forward to your reply. TKS

FutureEngineeer, 2023-11-12:
@ShenYuan-sean

This is a feature of the STM32G4. The joint use of USB and CAN functionality is only possible in this configuration.

However, this is not a problem. It is enough to set the nBOOT0 optional bit when loading the firmware and this makes it possible to use not the STM pin for bootloader mode, but the internal optional bit nSWBOOT0

I have tested this function and it definitely works

Closed 2023-11-12.

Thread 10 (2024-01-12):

Will we be getting a higher voltage driver (96+V)

hYdos, 2024-01-12:
It is a market no one is touching under $50. Having an affordable driver able to do this would open up higher speed and torque projects. Most nema 17 motor coils should be able to take at least 140V before they damage themselves.

TamaBaka, 2024-01-12:
This may require a complete redesign as a lot of the drive circuitry are specced for lower voltages than that.  Nevermind the trace separation needed.

FutureEngineeer, 2024-01-12:
@hYdos, I don't think it's worth the effort

I agree with @TamaBaka, usually drivers have up to 30V operating voltage and it's relatively easy to do.
For the 48V of the CLN17 V2.0 I had to try very hard to make the track gap about 0.375mm, although even that is not really enough to fully comply with the IPC2221A standards.
In the NEMA17 form factor I think 55V volts is close to the design limit, 100V seems impossible to me.
Plus it would be a lot more expensive, and there is little demand for such applications.

Maybe there will be such a possibility for CLN234, however there the limits will be 80V at best, and most likely the same 55V

So I don't plan to design for such high voltages (at least not in the foreseeable future)

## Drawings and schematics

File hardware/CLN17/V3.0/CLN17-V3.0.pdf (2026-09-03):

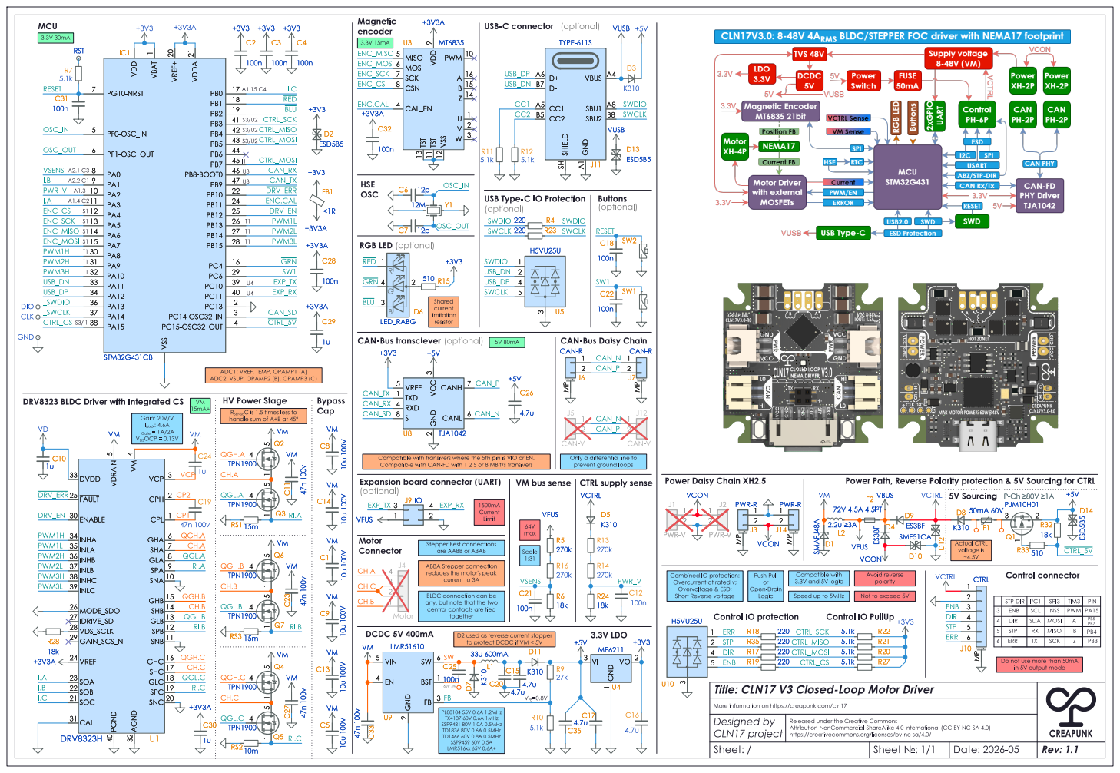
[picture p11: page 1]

1 VREF+ 20 VDDA 21 VDD VSS

CC2 RI.A QGL.A CH.A CH.B QGH.B

3.3V and 5V logic ADC1: VREF,TEMP,OPAMP1 (A) ADC2: VSUP,OPAMP2 (B), OPAMP3 (C) R_{SENSE}C is 1.5 times less to

Cap DRV8323 BLDCDriver with Integrated CS

handle sum of A+B at þÿ45° VM

Logic Only a differential line to

Expansion board connector (UART)
(optional) Motor Connector

Power Path, Reverse Polarity protection & 5V Sourcing for CTRL

together ABBA Stepper connection
reduces the motor's peak
current to 3A

in 5V output mode Speed up to 5MHz Compatible with

BLDC connection can be
any, but note that the two
central contacts are tied

Title:CLN17 V3 Closed-Loop Motor Driver

Sheet: / More information on https://creapunk.com/cln17 Designed by

CLN17 project
Released under the Creative Commons

https://creativecommons.org/licenses/by-nc-sa/4.0/ CREAPUNK

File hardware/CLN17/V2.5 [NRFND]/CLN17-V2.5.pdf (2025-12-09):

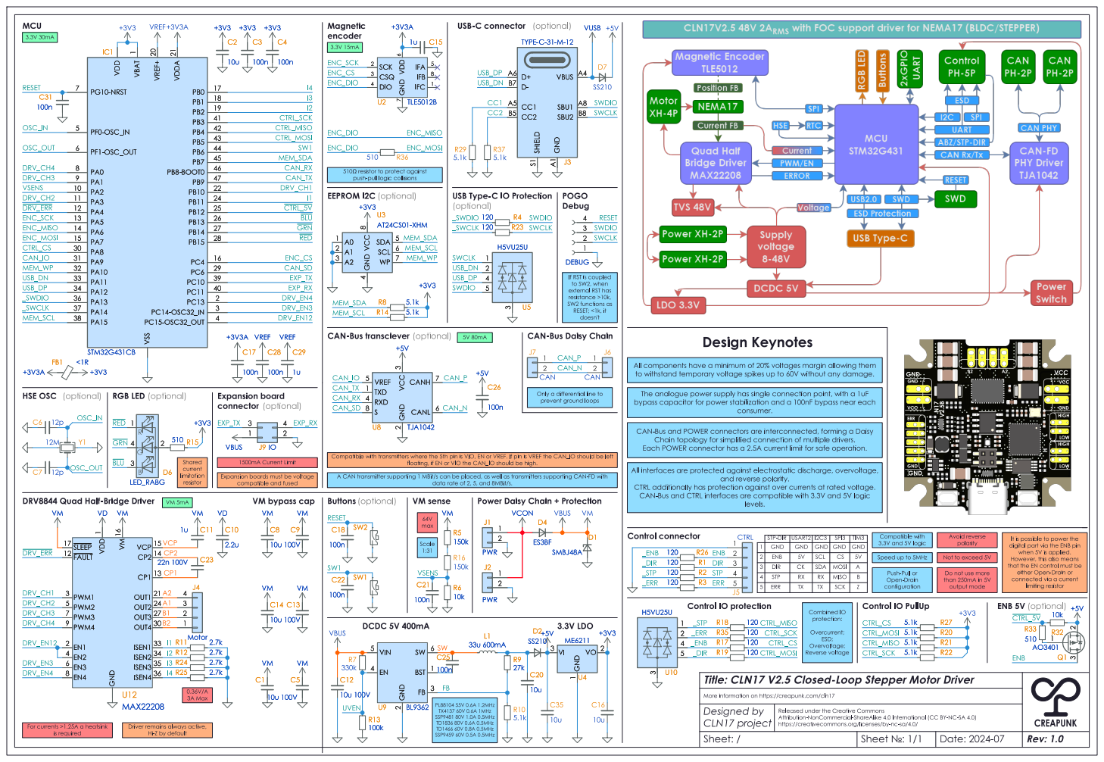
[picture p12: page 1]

1 VREF+ 20 VDDA 21 VDD VSS

protection: Overcurrent; ESD; Overvoltage; Reverse voltage All components have a minimum of 20% voltages margin allowing them
to withstand temporary voltage spikes up to 60V without any damage.

A MISO Buttons HSEOSC
prevent ground loops For currents >1.25A a heatsink

B MOSI ERR Expansion board
connector

The analogue power supply has single connection point, with a 1uF
bypass capacitor for power stabilization and a 100nF bypass near each

polarity Compatible with transmitters where the 5th pin isVIO, EN or VREF.If pin isVREFthe CAN_IO should be left

Expansion boards must be voltage

PL8810455V 0.6A 1.2MHz TX413760V 0.6A 1MHz SSP948180V 1.0A 0.5MHz TD183680V 0.6A 0.5MHz TD146660V 0.8A 0.5MHz SSP945960V 0.5A 0.5MHz A CAN transmitter supporting 1 MBit/s can be placed, as well as transmitters supporting CAN-FD with

limiting resistor Avoid reverse

It is possible to power the
digital part via the ENBpin when 5V is applied. However, this also means

output mode Speed up to 5MHz Push-Pull or Open-Drain

that the EN control must be
either Open-Drain or connected via a current

Title:CLN17 V2.5 Closed-Loop Stepper Motor Driver

Sheet: / More information on https://creapunk.com/cln17 Designed by

CLN17 project
Released under the Creative Commons

https://creativecommons.org/licenses/by-nc-sa/4.0/ CREAPUNK

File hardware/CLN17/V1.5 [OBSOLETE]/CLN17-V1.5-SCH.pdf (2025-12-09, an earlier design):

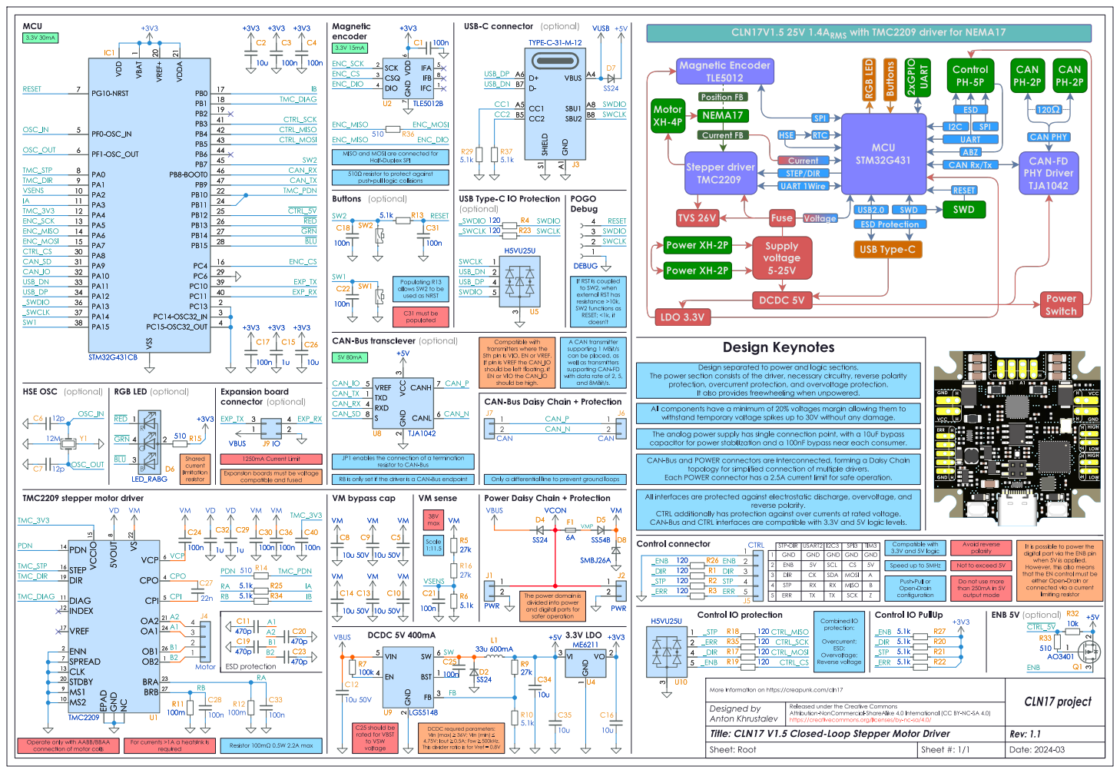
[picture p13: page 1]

1 VREF+ 20 VDDA 21 VDD VSS

þÿ510!& resistor to protect against push-pull logic collisions

1 Control IO protection Buttons

If RSTis coupled
to SW2,when
external RSThas
resistance >10k, SW2functions as RESET;<1k, it doesn't

with data rate of 2, 5, and 8MBit/s. Compatible with
transmitters where the
5th pin isVIO, EN or VREF.
If pin isVREFthe CAN_IO
should be left floating, if EN or VIO the CAN_IO

can be placed, as well as transmitters

protection, overcurrent protection, and overvoltage protection.

capacitor for power stabilization and a 100nF bypass near each consumer. CAN-Bus and POWERconnectors are interconnected, forming a Daisy Chain

output mode Speed up to 5MHz Shared
current
limitation

JP1 enables the connection of a termination

Expansion boards must be voltage

reverse polarity. CTRLadditionally has protection against over currents at rated voltage. CAN-Bus and CTRLinterfaces are compatible with 3.3V and 5V logic levels. C25 should be

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

polarity For currents >1A a heatsink is

that the EN control must be
either Open-Drain or connected via a current

limiting resistor Operate only with AABB/BBAA

The power domain is divided into power and digital parts for safer operation

protection: Overcurrent; ESD; Overvoltage; Reverse voltage

Designed by Anton | Released under the Creative Commons Khrustalev

DCDC requred parameters: Vin (max) þÿ"e36V; Vin (min) þÿ"d

https://creativecommons.org/licenses/by-nc-sa/4.0/ | | Date: 2024-03

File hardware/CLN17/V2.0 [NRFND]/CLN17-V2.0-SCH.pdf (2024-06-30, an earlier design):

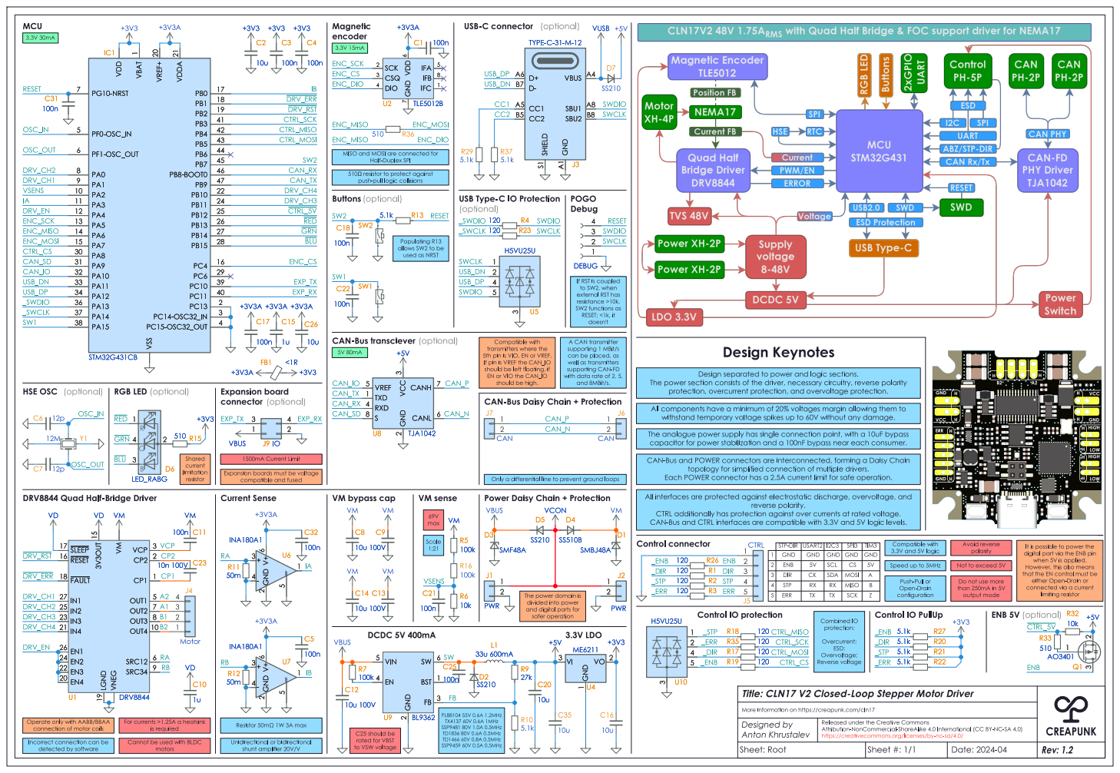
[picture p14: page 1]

1 VREF+ 20 VDDA 21 VDD VSS

MISO and MOSI are connected for Half-Duplex SPI Populating R13

USB_DP
_SWDIO
resistance >10k, SW2functions as RESET;<1k, it doesn't Operate only with AABB/BBAA
_SWCLK

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

can be placed, as well as transmitters

reverse polarity. CTRLadditionally has protection against over currents at rated voltage. CAN-Bus and CTRLinterfaces are compatible with 3.3V and 5V logic levels. Speed up to 5MHz Design separated to power and logic sections. The power section consists of the driver, necessary circuitry, reverse polarity

protection: Overcurrent; ESD; Overvoltage; Reverse voltage The analogue power supply has single connection point, with a 10uF bypass
capacitor for power stabilization and a 100nF bypass near each consumer.

output mode CAN-Bus and POWERconnectors are interconnected, forming a Daisy Chain
topology for simplified connection of multiple drivers. Each POWERconnector has a 2.5A current limit for safe operation.

1:21 Expansion boards must be voltage

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

5 SRC12
configuration Cannot be used with BLDC motors For currents >1.25A a heatsink

that the EN control must be
either Open-Drain or connected via a current

More information on https://creapunk.com/cln17 Title:CLN17 V2 Closed-Loop Stepper Motor Driver

connection of motor coils

Released under the Creative Commons

Incorrect connection can be

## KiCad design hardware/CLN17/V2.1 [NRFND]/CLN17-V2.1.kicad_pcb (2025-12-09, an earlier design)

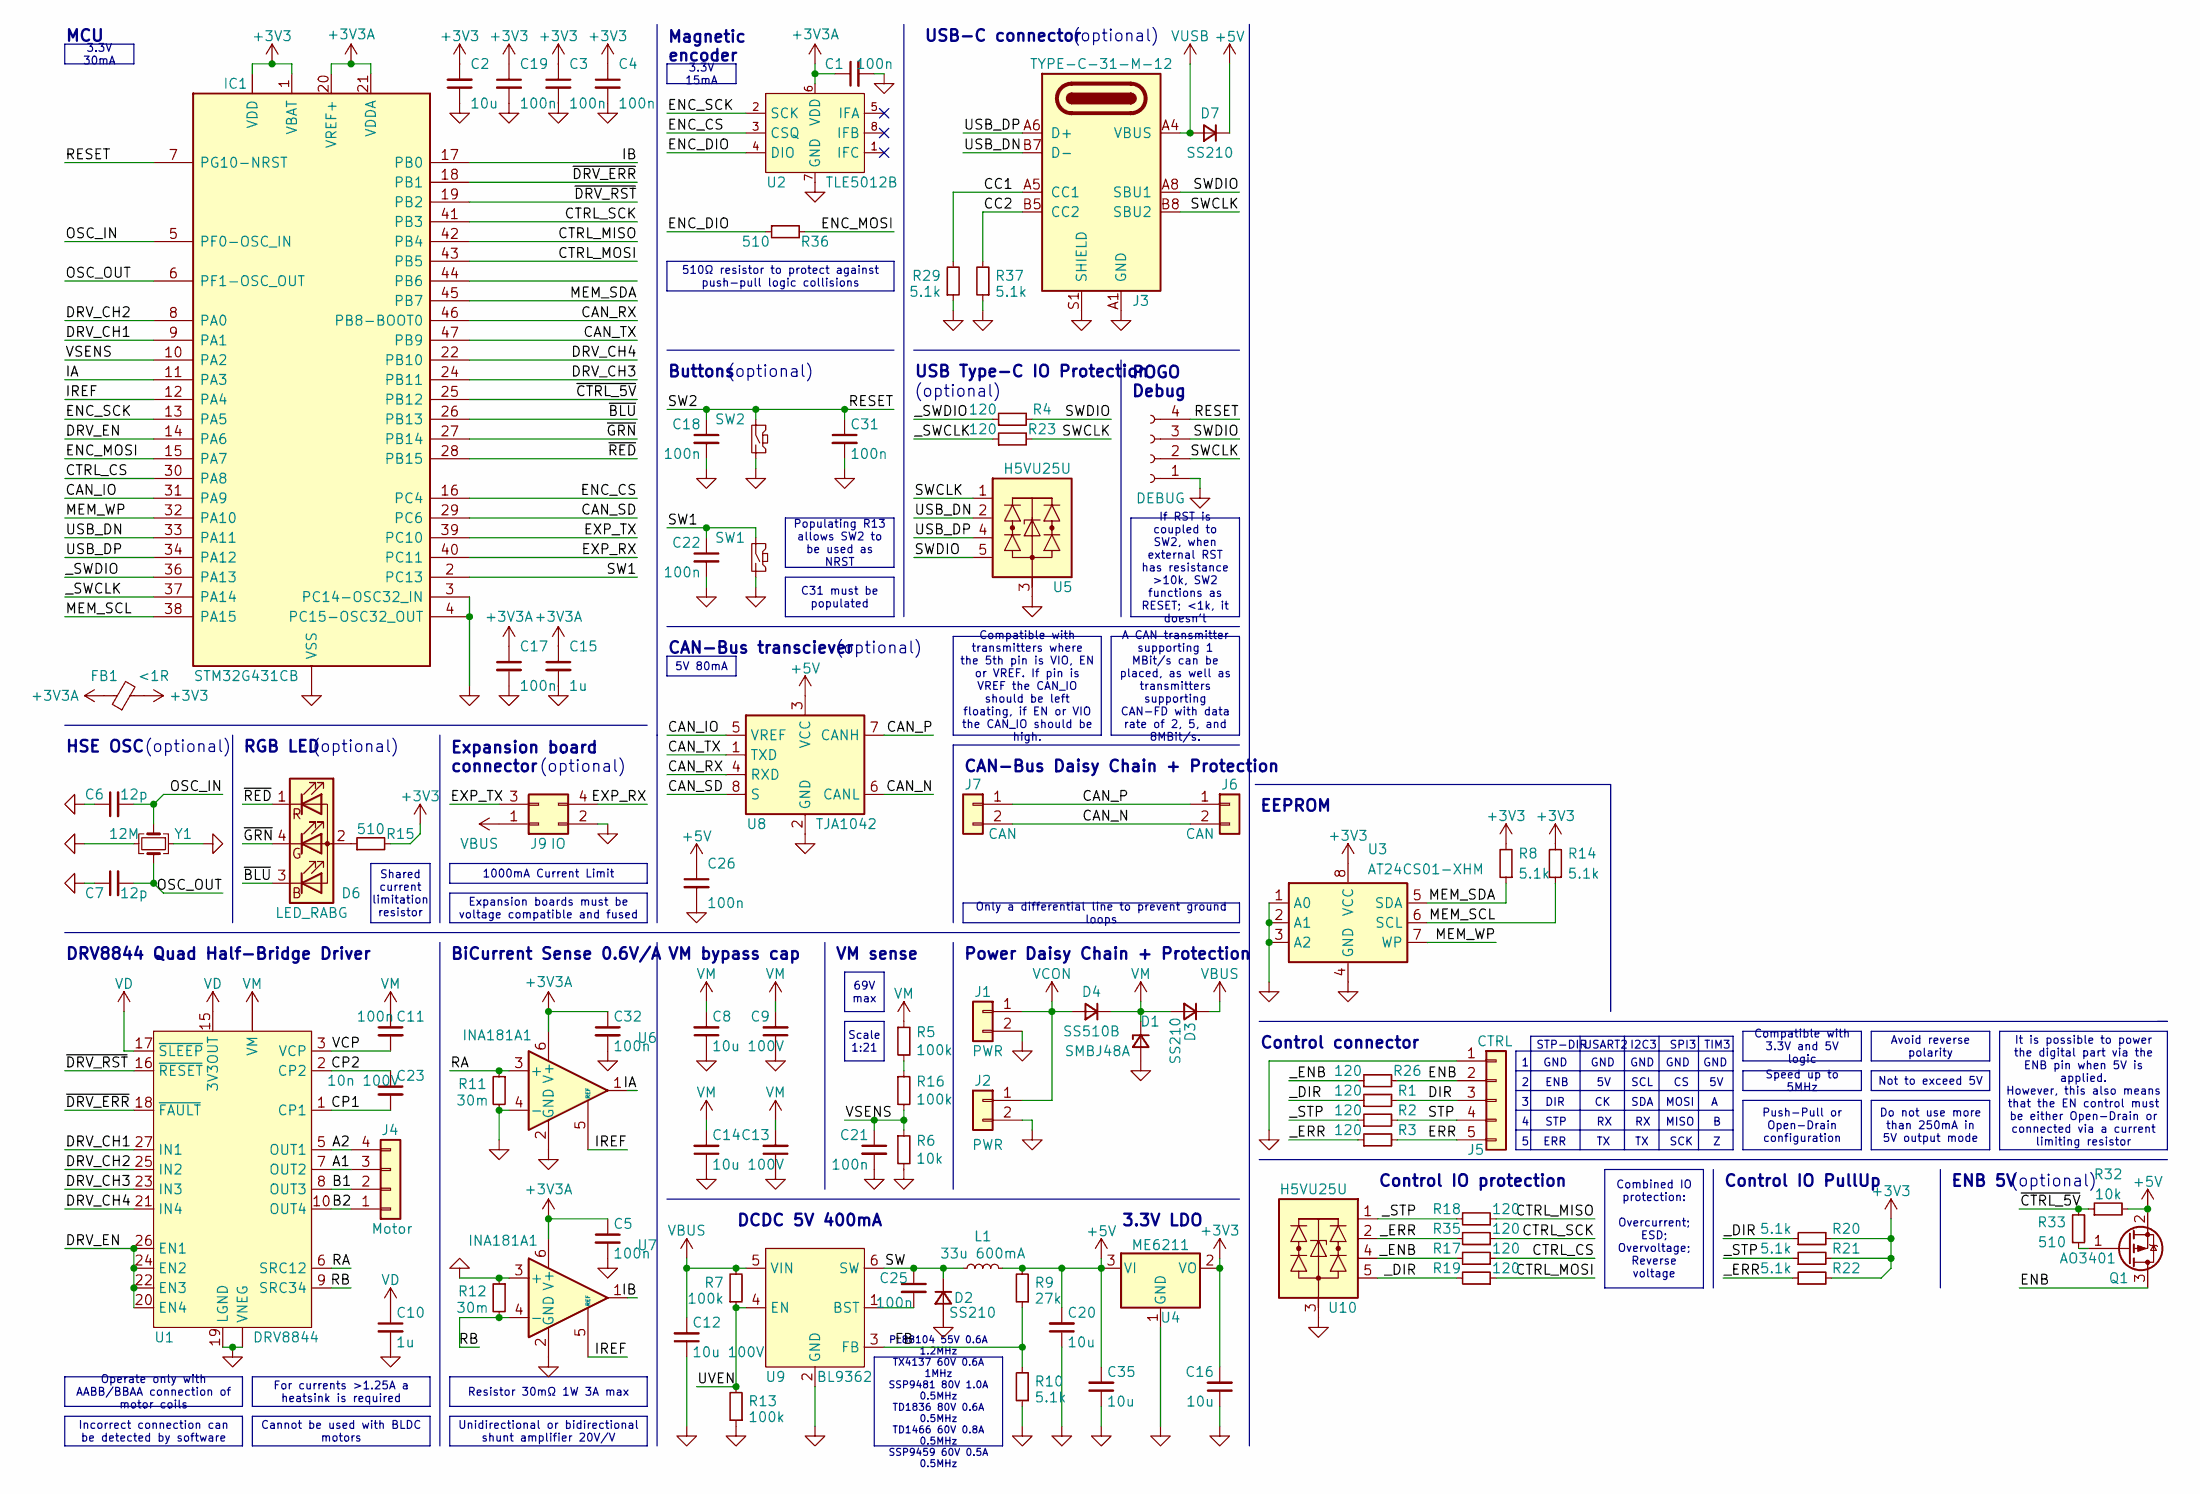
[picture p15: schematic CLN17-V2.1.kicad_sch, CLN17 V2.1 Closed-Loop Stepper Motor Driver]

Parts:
C1, C3, C4, C5, C11, C17, C18, C19, C21, C22, C25, C26, C31, C32: 100n; C0402; Part Type Basic; LCSC Part # C1525
C2, C16, C20, C35: 10u; C0402; Part Type Basic; LCSC Part # C15525
C6, C7: 12p; C0402; Part Type Basic; LCSC Part # C1547
C8, C9, C12, C13, C14: 10u 100V; C1210; Part Type Extended; LCSC Part # C5156756
C10, C15: 1u; C0402; Part Type Basic; LCSC Part # C52923
C23: 10n 100V; C0402; Part Type Extended; LCSC Part # C527014
D1: SMBJ48A; D_SMB; Part Type Extended; LCSC Part # C353356
D2, D3, D7: SS210; D_SOD-123F; Part Type Extended; LCSC Part # C183475
D4: SS510B; D_SMB; Part Type Extended; LCSC Part # C7420368
D6: LED_RABG; LED_RGB_0606; Part Type Extended; LCSC Part # C2874115
FB1: <1R; R0402; LCSC Part # C76883
IC1: STM32G431CB; QFN-48-1EP_7x7mm_P0.5mm_EP5.6x5.6mm; Part Type Extended; LCSC Part # C529356
J1, J2: PWR; XH2.54 2P; Part Type Extended; LCSC Part # C2908611
J3: TYPE-C-31-M-12; USB-TYPE-C-31-M-12; Part Type Extended; LCSC Part # C2988369
J4: Motor; XH2.54 4P; Part Type Extended; LCSC Part # C5188444
J5: CTRL; PH2.0 5P; Part Type Extended; LCSC Part # C2908637
J6, J7: CAN; PH2.0 2P; Part Type Extended; LCSC Part # C2908634
J8: DEBUG; SWD; Part Type -----
J9: IO; 2x2P2.00mm_Vertical_SMD; Part Type Extended; LCSC Part # C2911301
L1: 33u 600mA; CD32; Part Type Extended; LCSC Part # C492262
Q1: AO3401; SOT-23-3; Part Type Basic; LCSC Part # C15127
R1, R2, R3, R4, R17, R18, R19, R23, R26, R35: 120; R0402; Part Type Basic; LCSC Part # C25079
R5, R7, R13, R16: 100k; R0402; Part Type Basic; LCSC Part # C25741
R6, R32: 10k; R0402; Part Type Basic; LCSC Part # C25744
R8, R10, R14, R20, R21, R22, R29, R37: 5.1k; R0402; Part Type Basic; LCSC Part # C25941
R9: 27k; R0402; Part Type Basic; LCSC Part # C25771
R11, R12: 30m; R1206_Shunt; Part Type Extended; LCSC Part # C7467247
R15, R33, R36: 510; R0402; Part Type Basic; LCSC Part # C25123
SW1, SW2: SW_Push; SW_SPST_PTS810; Part Type Extended; LCSC Part # C2888430
U1: DRV8844; HTSSOP-28-1EP_4.4x9.7mm_P0.65mm_EP2.85x5.4mm; Part Type Extended; LCSC Part # C177807
U2: TLE5012B; SOIC-8_3.9x4.9mm_P1.27mm; Part Type Extended; LCSC Part # C123083
U3: AT24CS01-XHM; MSOP-TSSOP-8-P0.65mm
U4: ME6211; SOT-23-3; Part Type Basic; LCSC Part # C168807
U5, U10: H5VU25U; DFN-2510; Part Type Basic; LCSC Part # C7420374
U6, U7: INA181A1; SOT-23-6; LCSC Part # C2058943
U8: TJA1042; HVSON-8-1EP_3x3mm_P0.65mm_EP1.6x2.4mm; Part Type Extended; LCSC Part # C131480
U9: BL9362; SOT-23-6; Part Type Extended; LCSC Part # C2909086
Y1: 12M; Oscillator_SMD_Kyocera_KC2520Z-4Pin_2.5x2.0mm; Part Type Basic; LCSC Part # C9002

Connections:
+3V3: C2.2, C3.1, C4.1, C16.2, C19.1, FB1.2, IC1.1 (VBAT), IC1.23 (VDD), IC1.35 (VDD), IC1.48 (VDD), R8.2, R14.2, R15.2, R20.2, R21.2, R22.2, U3.8 (VCC), U4.2 (VO)
+3V3A: C1.1, C5.1, C15.1, C17.1, C32.1, FB1.1, IC1.20 (VREF+), IC1.21 (VDDA), U2.6 (VDD), U6.6 (V+), U7.6 (V+)
+5V: C20.2, C26.1, C35.2, D7.1 (K), L1.2, Q1.2 (S), R9.2, R32.2, U4.3 (VI), U8.3 (VCC)
/A1: J4.3, U1.7 (OUT2)
/A2: J4.4, U1.5 (OUT1)
/B1: J4.2, U1.8 (OUT3)
/B2: J4.1, U1.10 (OUT4)
/CAN_IO: IC1.31 (PA9), U8.5 (VREF)
/CAN_N: J6.2, J7.2, U8.6 (CANL)
/CAN_P: J6.1, J7.1, U8.7 (CANH)
/CAN_RX: IC1.46 (PB8-BOOT0), U8.4 (RXD)
/CAN_SD: IC1.29 (PC6), U8.8 (S)
/CAN_TX: IC1.47 (PB9), U8.1 (TXD)
/CC1: J3.A5 (CC1), R29.2
/CC2: J3.B5 (CC2), R37.2
/CP1: C23.2, U1.1 (CP1)
/CP2: C23.1, U1.2 (CP2)
/CTRL_CS: IC1.30 (PA8), R17.1
/CTRL_MISO: IC1.42 (PB4), R18.1
/CTRL_MOSI: IC1.43 (PB5), R19.1
/CTRL_SCK: IC1.41 (PB3), R35.1
/DIR: J5.3, R1.2
/DRV_CH1: IC1.9 (PA1), U1.27 (IN1)
/DRV_CH2: IC1.8 (PA0), U1.25 (IN2)
/DRV_CH3: IC1.24 (PB11), U1.23 (IN3)
/DRV_CH4: IC1.22 (PB10), U1.21 (IN4)
/DRV_EN: IC1.14 (PA6), U1.20 (EN4), U1.22 (EN3), U1.24 (EN2), U1.26 (EN1)
/ENB: J5.2, Q1.3 (D), R26.2
/ENC_CS: IC1.16 (PC4), U2.3 (CSQ)
/ENC_DIO: R36.1, U2.4 (DIO)
/ENC_MOSI: IC1.15 (PA7), R36.2
/ENC_SCK: IC1.13 (PA5), U2.2 (SCK)
/ERR: J5.5, R3.2
/EXP_RX: IC1.40 (PC11), J9.4
/EXP_TX: IC1.39 (PC10), J9.3
/FB: R9.1, R10.2, U9.3 (FB)
/IA: IC1.11 (PA3), U6.1
/IB: IC1.17 (PB0), U7.1
/IREF: IC1.12 (PA4), U6.5 (REF), U7.5 (REF)
/MEM_SCL: IC1.38 (PA15), R14.1, U3.6 (SCL)
/MEM_SDA: IC1.45 (PB7), R8.1, U3.5 (SDA)
/MEM_WP: IC1.32 (PA10), U3.7 (WP)
/OSC_IN: C6.2, IC1.5 (PF0-OSC_IN), Y1.1
/OSC_OUT: C7.2, IC1.6 (PF1-OSC_OUT), Y1.3
/RA: R11.1, U1.6 (SRC12), U6.3 (+)
/RB: R12.2, U1.9 (SRC34), U7.4 (-)
/RESET: C18.1, C31.1, IC1.7 (PG10-NRST), J8.4, SW2.1
/STP: J5.4, R2.2
/SW: C25.1, D2.1 (K), L1.1, U9.6 (SW)
/SW1: C22.1, IC1.2 (PC13), SW1.1
/SWCLK: J3.B8 (SBU2), J8.2, R23.2, U5.1 (I/O1), U5.10
/SWDIO: J3.A8 (SBU1), J8.3, R4.2, U5.5 (I/O4), U5.6 (I/O4)
/USB_DN: IC1.33 (PA11), J3.A7 (D-), J3.B7 (D-), U5.2 (I/O2), U5.9 (I/O2)
/USB_DP: IC1.34 (PA12), J3.A6 (D+), J3.B6 (D+), U5.4 (I/O3), U5.7 (I/O3)
/UVEN: R7.1, R13.2, U9.4 (EN)
/VCP: C11.2, U1.3 (VCP)
/VSENS: C21.1, IC1.10 (PA2), R6.1, R16.2
/_DIR: R1.1, R19.2, R20.1, U10.5 (I/O4), U10.6 (I/O4)
/_ENB: R17.2, R26.1, U10.4 (I/O3), U10.7 (I/O3)
/_ERR: R3.1, R22.1, R35.2, U10.2 (I/O2), U10.9 (I/O2)
/_STP: R2.1, R18.2, R21.1, U10.1 (I/O1), U10.10
/_SWCLK: IC1.37 (PA14), R23.1
/_SWDIO: IC1.36 (PA13), R4.1
/~BLU: D6.3 (BK), IC1.26 (PB13)
/~CTRL_5V: IC1.25 (PB12), R32.1, R33.2
/~DRV_ERR: IC1.18 (PB1), U1.18 (~FAULT)
/~DRV_RST: IC1.19 (PB2), U1.16 (~RESET)
/~GRN: D6.4 (GK), IC1.27 (PB14)
/~RED: D6.1 (RK), IC1.28 (PB15)
GND: C1.2, C2.1, C3.2, C4.2, C5.2, C6.1, C7.1, C8.1, C9.1, C10.2, C12.1, C13.1, C14.1, C15.2, C16.1, C17.2, C18.2, C19.2, C20.1, C21.2, C22.2, C26.2, C31.2, C32.2, C35.1, D1.2 (A), D2.2 (A), IC1.3 (PC14-OSC32_IN), IC1.4 (PC15-OSC32_OUT), IC1.49 (VSS), J1.2, J2.2, J3.A1 (GND), J3.A12 (GND), J3.B1 (GND), J3.B12 (GND), J3.S1 (SHIELD), J5.1, J8.1, J9.2, R6.2, R10.1, R11.2, R12.1, R13.1, R29.1, R37.1, SW1.2, SW2.2, U1.14 (VNEG), U1.19 (LGND), U1.28 (VNEG), U1.29 (VNEG), U2.7 (GND), U3.1 (A0), U3.2 (A1), U3.3 (A2), U3.4 (GND), U4.1 (GND), U5.3 (GND), U5.8 (GND), U6.2 (GND), U6.4 (-), U7.2 (GND), U7.3 (+), U8.2 (GND), U8.9 (GND), U9.2 (GND), U10.3 (GND), U10.8 (GND), Y1.2, Y1.4
unnamed: D6.2 (A), R15.1
unnamed: Q1.1 (G), R33.1
unnamed: R5.2, R16.1
unnamed: C25.2, U9.1 (BST)
VBUS: C12.2, D3.1 (K), J9.1, R7.2, U9.5 (VIN)
VCON: D4.2 (A), J1.1, J2.1
VD: C10.1, U1.15 (3V3OUT), U1.17 (~SLEEP)
VM: C8.2, C9.2, C11.1, C13.2, C14.2, D1.1 (K), D3.2 (A), D4.1 (K), R5.1, U1.4 (VM), U1.11 (VM)
VUSB: D7.2 (A), J3.A4 (VBUS), J3.A9 (VBUS), J3.B4 (VBUS), J3.B9 (VBUS)

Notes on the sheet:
Operate only with AABB/BBAA connection of motor coils
Combined IO protection: Overcurrent; ESD; Overvoltage; Reverse voltage
Cannot be used with BLDC motors
Only a differential line to prevent ground loops
Do not use more than 250mA in 5V output mode
3.3V 30mA
A CAN transmitter supporting 1 MBit/s can be placed, as well as transmitters supporting CAN-FD with data rate of 2, 5, and 8MBit/s.
If RST is coupled to SW2, when external RST has resistance >10k, SW2 functions as RESET; <1k, it doesn't
C31 must be populated
Speed up to 5MHz
Shared current limitation resistor
Expansion boards must be voltage compatible and fused
Compatible with 3.3V and 5V logic
It is possible to power the digital part via the ENB pin when 5V is applied. However, this also means that the EN control must be either Open-Drain or connected via a current limiting resistor
Unidirectional or bidirectional shunt amplifier 20V/V
Scale 1:21
Compatible with transmitters where the 5th pin is VIO, EN or VREF. If pin is VREF the CAN_IO should be left floating, if EN or VIO the CAN_IO should be high.
3.3V 15mA
Incorrect connection can be detected by software
PL88104 55V 0.6A 1.2MHz TX4137 60V 0.6A 1MHz SSP9481 80V 1.0A 0.5MHz TD1836 80V 0.6A 0.5MHz TD1466 60V 0.8A 0.5MHz SSP9459 60V 0.5A 0.5MHz
5V 80mA
Populating R13 allows SW2 to be used as NRST
1000mA Current Limit
Push-Pull or Open-Drain configuration
Resistor 30mΩ 1W 3A max
Not to exceed 5V
69V max
510Ω resistor to protect against push-pull logic collisions
For currents >1.25A a heatsink is required
Avoid reverse polarity
STP-DIR
CAN-Bus Daisy Chain + Protection
(optional)
GND
SPI3
Magnetic encoder
I2C3
USART2
MISO
MCU

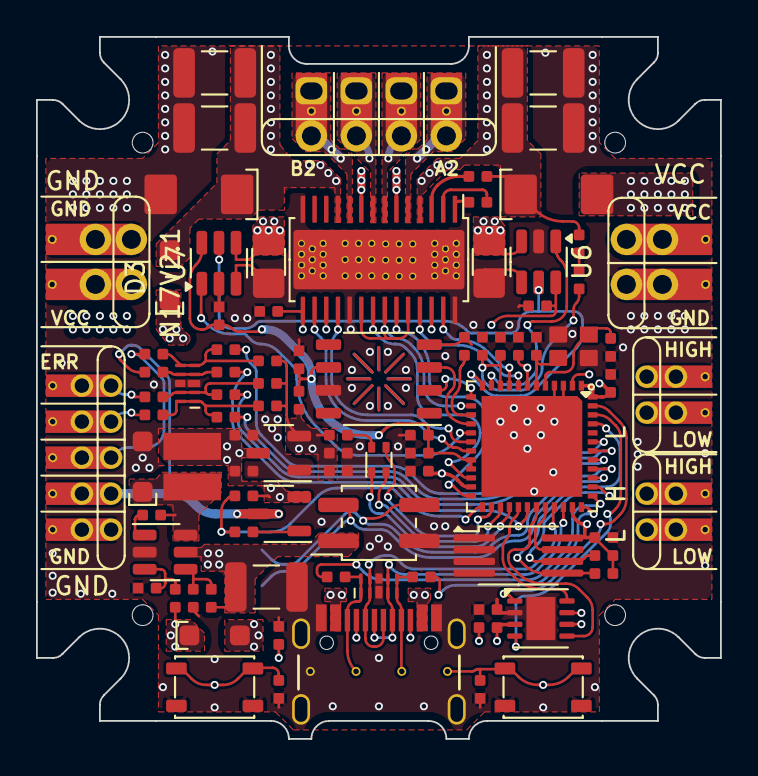
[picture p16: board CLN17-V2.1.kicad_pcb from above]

Board: 4 copper layers, 38.0 x 39.0 mm, 90 parts (1 on the bottom side), 79 nets.

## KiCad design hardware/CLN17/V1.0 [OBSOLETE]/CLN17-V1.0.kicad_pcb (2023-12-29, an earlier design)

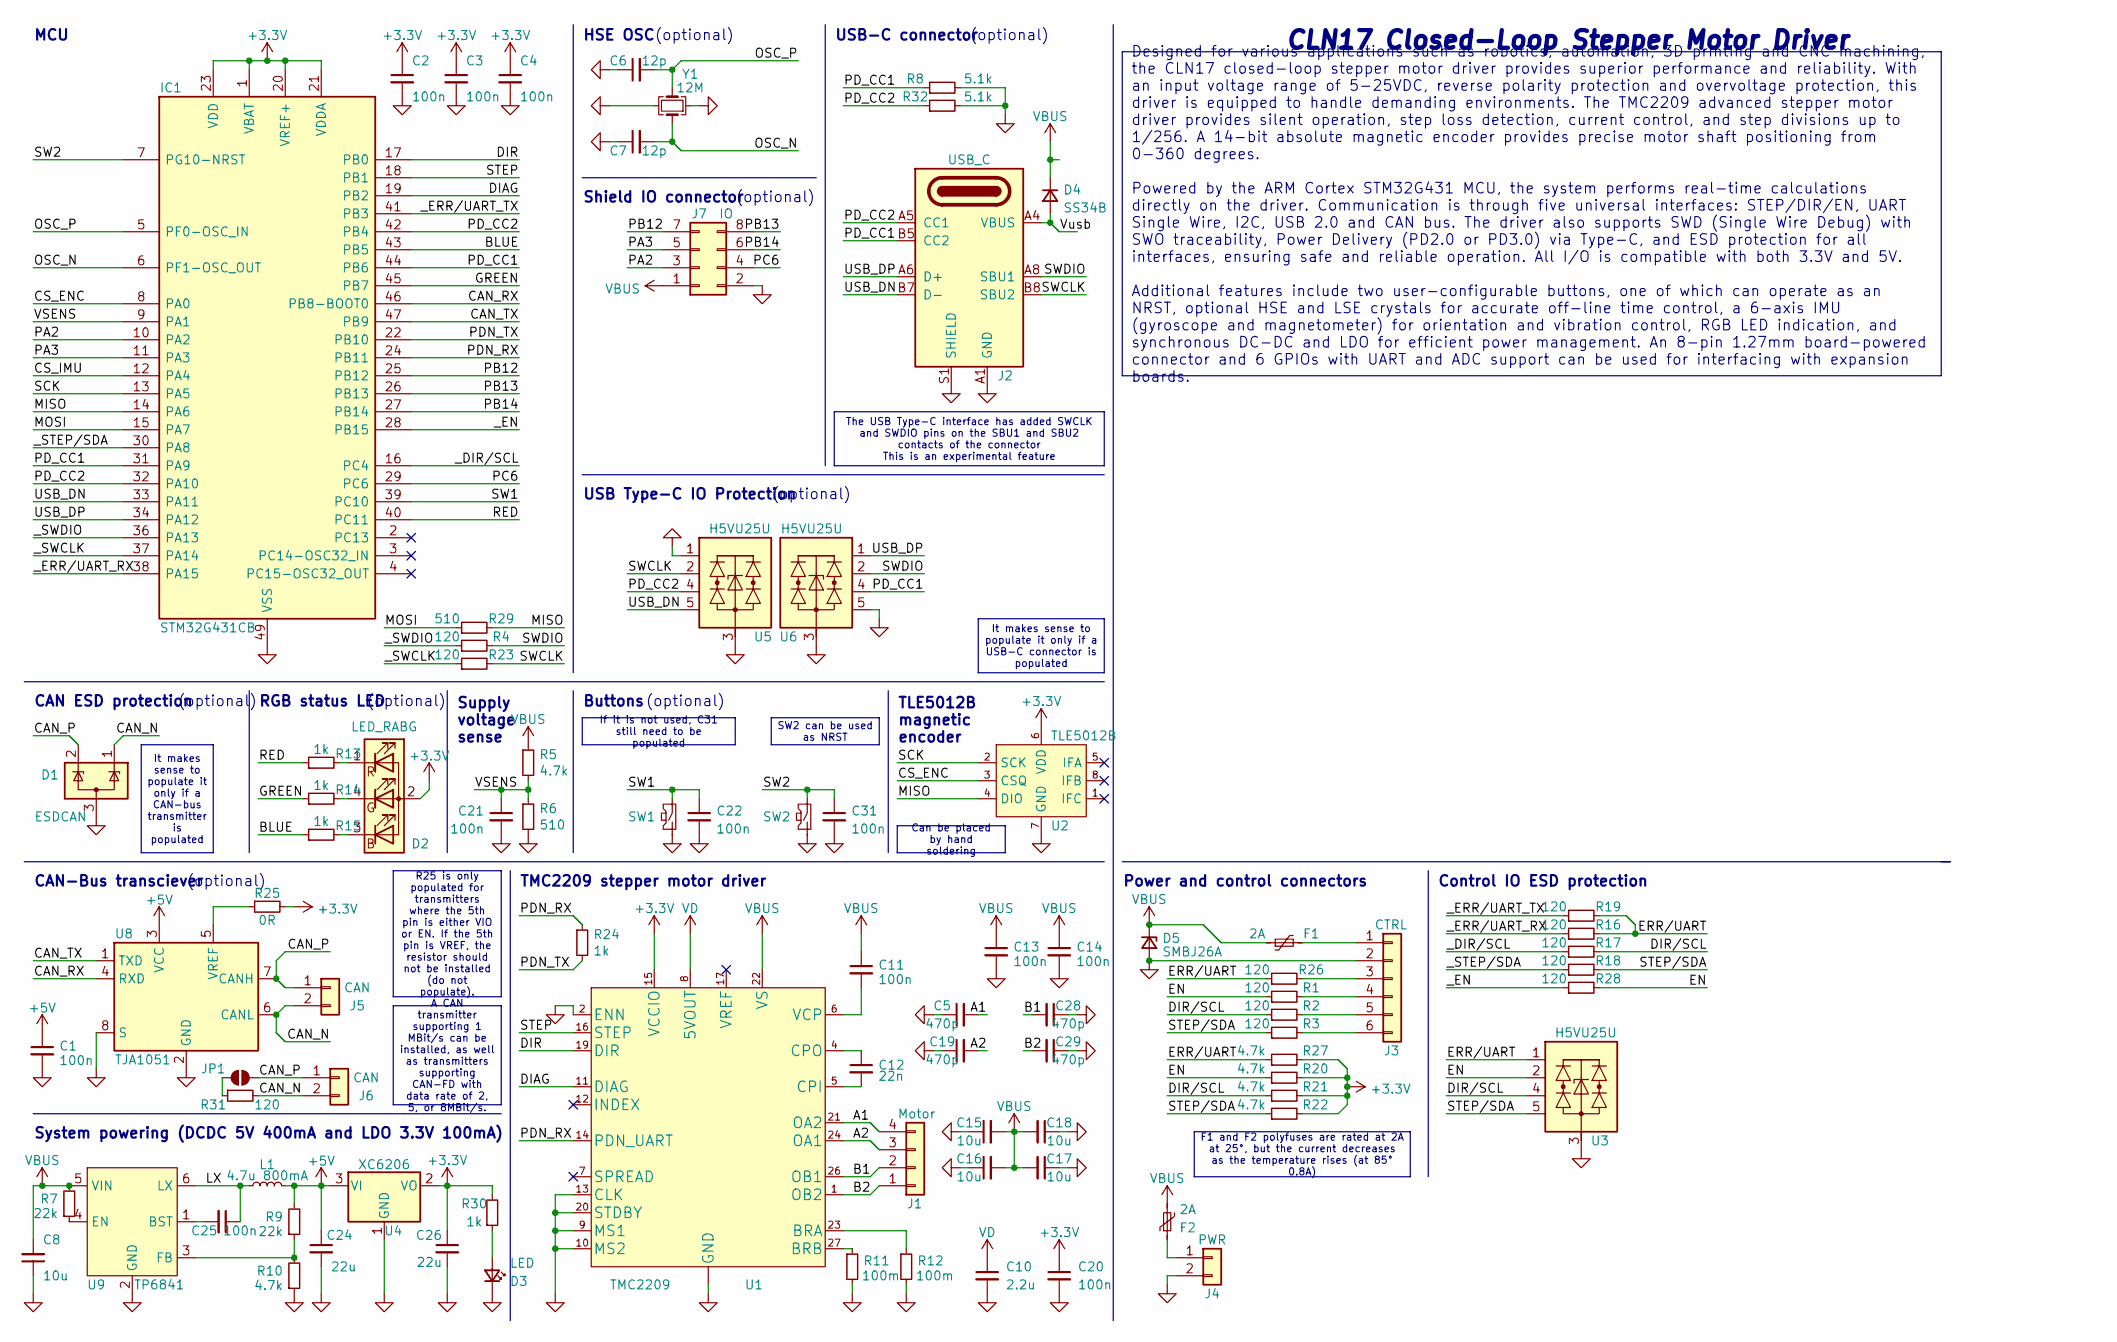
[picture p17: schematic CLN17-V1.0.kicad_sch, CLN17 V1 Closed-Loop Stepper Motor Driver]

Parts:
C1, C2, C3, C4, C11, C13, C14, C20, C21, C22, C25, C31: 100n; C0402; LCSC Part # C307331
C5, C19, C28, C29: 470p; C0402; LCSC Part # C1537
C6, C7: 12p; C0402; LCSC Part # C1547
C8, C15, C16, C17, C18: 10u; C_1206_3216Metric; LCSC Part # C13585
C10: 2.2u; C_0603_1608Metric; LCSC Part # C23630
C12: 22n; C0402; LCSC Part # C1532
C24, C26: 22u; C_0603_1608Metric; LCSC Part # C59461
D1: ESDCAN; SOT-23-3; LCSC Part # C2937021
D2: LED_RABG; LED_RGB_0606; LCSC Part # C2874115
D3: LED; LED_0603_1608Metric; LCSC Part # C72043
D4: SS34B; D_SMB; LCSC Part # C13762
D5: SMBJ26A; D_SMB; LCSC Part # C708006
F1, F2: 2A; Fuse_1812_4532Metric; LCSC Part # C960026
IC1: STM32G431CB; QFN-48-1EP_7x7mm_P0.5mm_EP5.6x5.6mm; LCSC Part # C529356
J1: Motor; XH2.54 4P; LCSC Part # C722872
J2: USB_C; USB-TYPE-C-31-M-12-SWD; LCSC Part # C963413
J3: CTRL; XH2.54 6P; LCSC Part # C722881
J4: PWR; XH2.54 2P; LCSC Part # C722860
J5, J6: CAN; PH2.0 2P; LCSC Part # C2908634
J7: IO; PinSocket_2x04_P1.27mm_Vertical; LCSC Part # C509139
JP1: SolderJumper_2_Open; SolderJumper
L1: 4.7u 800mA; L_0805_2012Metric; LCSC Part # C63166
R1, R2, R3, R4, R16, R17, R18, R19, R23, R26, R28, R31: 120; R0402; LCSC Part # C25079
R5, R10, R20, R21, R22, R27: 4.7k; R0402; LCSC Part # C25900
R6, R29: 510; R0402; LCSC Part # C25123
R7, R9: 22k; R0402; LCSC Part # C25768
R8, R32: 5.1k; R0402; LCSC Part # C25905
R11, R12: 100m; R_1206_3216Metric; LCSC Part # C25334
R13, R14, R15, R24, R30: 1k; R0402; LCSC Part # C11702
R25: 0R; R0402; LCSC Part # C17168
SW1, SW2: SW_Push; SW_SPST_PTS810; LCSC Part # C2888427
U1: TMC2209; QFN-28-termal; LCSC Part # C465949
U2: TLE5012B; SOIC-8_3.9x4.9mm_P1.27mm; LCSC Part # C123083
U3, U5, U6: H5VU25U; DFN-2510; JLC Rotation Offset 270
U4: XC6206; SOT-23-3; LCSC Part # C5446
U8: TJA1051; SOIC-8_3.9x4.9mm_P1.27mm; LCSC Part # C92211
U9: TP6841; SOT-23-6; LCSC Part # C2844736
Y1: 12M; Crystal-3225-4P; LCSC Part # C9002

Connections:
+3V3: C2.1, C3.1, C4.1, C20.1, C26.1, D2.2 (A), IC1.1 (VBAT), IC1.20 (VREF+), IC1.21 (VDDA), IC1.23 (VDD), IC1.35 (VDD), IC1.48 (VDD), R20.2, R21.2, R22.2, R25.2, R27.2, R30.2, U1.15 (VCCIO), U2.6 (VDD), U4.2 (VO)
+5V: C1.1, C24.1, L1.2, R9.2, U4.3 (VI), U8.3 (VCC)
/A1: C5.2, J1.4, U1.21 (OA2)
/A2: C19.2, J1.3, U1.24 (OA1)
/B1: C28.2, J1.2, U1.26 (OB1)
/B2: C29.2, J1.1, U1.1 (OB2)
/BLUE: IC1.43 (PB5), R15.1
/CAN_N: D1.1 (K), J5.2, J6.2, R31.2, U8.6 (CANL)
/CAN_P: D1.2 (K), J5.1, J6.1, JP1.2 (B), U8.7 (CANH)
/CAN_RX: IC1.46 (PB8-BOOT0), U8.4 (RXD)
/CAN_TX: IC1.47 (PB9), U8.1 (TXD)
/CS_ENC: IC1.8 (PA0), U2.3 (CSQ)
/CS_IMU: IC1.12 (PA4)
/DIAG: IC1.19 (PB2), U1.11 (DIAG)
/DIR: IC1.17 (PB0), U1.19 (DIR)
/DIR/SCL: R2.1, R17.2, R21.1, U3.4 (I/O3), U3.7 (I/O3)
/EN: R1.1, R20.1, R28.2, U3.2 (I/O2), U3.9 (I/O2)
/ERR/UART: R16.2, R19.2, R26.1, R27.1, U3.1 (I/O1), U3.10
/GREEN: IC1.45 (PB7), R14.1
/LX: C25.1, L1.1, U9.6 (LX)
/MISO: IC1.14 (PA6), R29.2, U2.4 (DIO)
/MOSI: IC1.15 (PA7), R29.1
/OSC_N: C7.2, IC1.6 (PF1-OSC_OUT), Y1.1
/OSC_P: C6.2, IC1.5 (PF0-OSC_IN), Y1.3
/PA2: IC1.10 (PA2), J7.3
/PA3: IC1.11 (PA3), J7.5
/PB12: IC1.25 (PB12), J7.7
/PB13: IC1.26 (PB13), J7.8
/PB14: IC1.27 (PB14), J7.6
/PC6: IC1.29 (PC6), J7.4
/PDN_RX: IC1.24 (PB11), R24.1, U1.14 (PDN_UART)
/PDN_TX: IC1.22 (PB10), R24.2
/PD_CC1: IC1.31 (PA9), IC1.44 (PB6), J2.B5 (CC2), R8.1, U6.4 (I/O3), U6.7 (I/O3)
/PD_CC2: IC1.32 (PA10), IC1.42 (PB4), J2.A5 (CC1), R32.1, U5.4 (I/O3), U5.7 (I/O3)
/RED: IC1.40 (PC11), R13.1
/SCK: IC1.13 (PA5), U2.2 (SCK)
/STEP: IC1.18 (PB1), U1.16 (STEP)
/STEP/SDA: R3.1, R18.2, R22.1, U3.5 (I/O4), U3.6 (I/O4)
/SW1: C22.1, IC1.39 (PC10), SW1.1
/SW2: C31.1, IC1.7 (PG10-NRST), SW2.1
/SWCLK: J2.B8 (SBU2), R23.2, U5.2 (I/O2), U5.9 (I/O2)
/SWDIO: J2.A8 (SBU1), R4.2, U6.2 (I/O2), U6.9 (I/O2)
/USB_DN: IC1.33 (PA11), J2.A7 (D-), J2.B7 (D-), U5.5 (I/O4), U5.6 (I/O4)
/USB_DP: IC1.34 (PA12), J2.A6 (D+), J2.B6 (D+), U6.1 (I/O1), U6.10
/VSENS: C21.1, IC1.9 (PA1), R5.2, R6.1
/Vusb: D4.2 (A), J2.A4 (VBUS), J2.A9 (VBUS), J2.B4 (VBUS), J2.B9 (VBUS)
/_DIR/SCL: IC1.16 (PC4), R17.1
/_EN: IC1.28 (PB15), R28.1
/_ERR/UART_RX: IC1.38 (PA15), R16.1
/_ERR/UART_TX: IC1.41 (PB3), R19.1
/_STEP/SDA: IC1.30 (PA8), R18.1
/_SWCLK: IC1.37 (PA14), R23.1
/_SWDIO: IC1.36 (PA13), R4.1
GND: C1.2, C2.2, C3.2, C4.2, C5.1, C6.1, C7.1, C8.1, C10.2, C13.2, C14.2, C15.1, C16.1, C17.1, C18.1, C19.1, C20.2, C21.2, C22.2, C24.2, C26.2, C28.1, C29.1, C31.2, D1.3 (A), D3.1 (K), D5.2 (A), IC1.49 (VSS), J2.A1 (GND), J2.A12 (GND), J2.B1 (GND), J2.B12 (GND), J2.S1 (SHIELD), J3.2, J4.2, J7.2, R6.2, R8.2, R10.1, R11.2, R12.2, R32.2, SW1.2, SW2.2, U1.2 (ENN), U1.3 (GND), U1.9 (MS1), U1.10 (MS2), U1.13 (CLK), U1.18 (GND), U1.20 (STDBY), U1.25 (NC), U1.29 (EPAD), U2.7 (GND), U3.3 (GND), U3.8 (GND), U4.1 (GND), U5.1 (I/O1), U5.3 (GND), U5.8 (GND), U5.10, U6.3 (GND), U6.5 (I/O4), U6.6 (I/O4), U6.8 (GND), U8.2 (GND), U8.8 (S), U9.2 (GND), Y1.2, Y1.4
unnamed: D2.3 (BK), R15.2
unnamed: D2.4 (GK), R14.2
unnamed: D2.1 (RK), R13.2
unnamed: D3.2 (A), R30.1
unnamed: F1.2, J3.1
unnamed: J3.3, R26.2
unnamed: J3.4, R1.2
unnamed: J3.5, R2.2
unnamed: J3.6, R3.2
unnamed: F2.1, J4.1
unnamed: JP1.1 (A), R31.1
unnamed: R12.1, U1.23 (BRA)
unnamed: R11.1, U1.27 (BRB)
unnamed: C12.2, U1.5 (CPI)
unnamed: C12.1, U1.4 (CPO)
unnamed: C11.2, U1.6 (VCP)
unnamed: R25.1, U8.5 (VREF)
unnamed: C25.2, U9.1 (BST)
unnamed: R7.1, U9.4 (EN)
unnamed: R9.1, R10.2, U9.3 (FB)
VBUS: C8.2, C11.1, C13.1, C14.1, C15.2, C16.2, C17.2, C18.2, D4.1 (K), D5.1 (K), F1.1, F2.2, J7.1, R5.1, R7.2, U1.22 (VS), U1.28 (VS), U9.5 (VIN)
VD: C10.1, U1.8 (5VOUT)

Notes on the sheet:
R25 is only populated for transmitters where the 5th pin is either VIO or EN. If the 5th pin is VREF, the resistor should not be installed (do not populate).
Can be placed by hand soldering
A CAN transmitter supporting 1 MBit/s can be installed, as well as transmitters supporting CAN-FD with data rate of 2, 5, or 8MBit/s.
If it is not used, C31 still need to be populated
The USB Type-C interface has added SWCLK and SWDIO pins on the SBU1 and SBU2 contacts of the connector This is an experimental feature
It makes sense to populate it only if a CAN-bus transmitter is populated
SW2 can be used as NRST
F1 and F2 polyfuses are rated at 2A at 25°, but the current decreases as the temperature rises (at 85° 0.8A)
It makes sense to populate it only if a USB-C connector is populated
Designed for various applications such as robotics, automation, 3D printing and CNC machining, the CLN17 closed-loop stepper motor driver provides superior performance and reliability. With an input voltage range of 5-25VDC, reverse polarity protection and overvoltage protection, this driver is equ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
(optional)
CLN17 Closed-Loop Stepper Motor Driver
TLE5012B magnetic encoder
MCU
CAN-Bus transciever
Power and control connectors
System powering (DCDC 5V 400mA and LDO 3.3V 100mA)
CAN ESD protection
Shield IO connector
USB-C connector
TMC2209 stepper motor driver
Buttons
RGB status LED
Supply voltage sense
HSE OSC
Control IO ESD protection
USB Type-C IO Protection

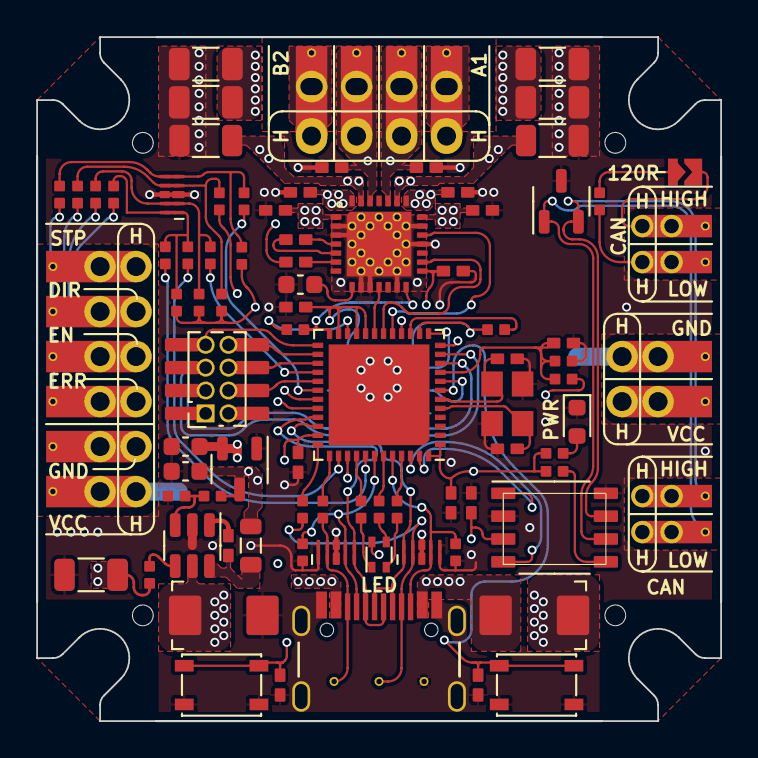
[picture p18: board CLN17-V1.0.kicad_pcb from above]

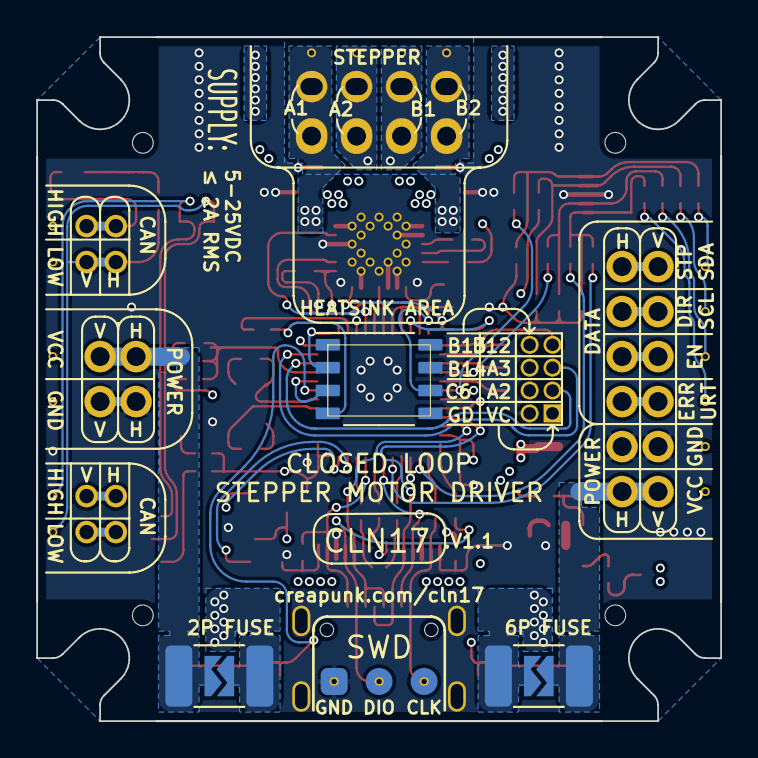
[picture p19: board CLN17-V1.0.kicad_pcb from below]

Board: 4 copper layers, 38.0 x 38.0 mm, 87 parts (3 on the bottom side), 75 nets.

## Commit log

2023-10-10 CLN17 V1 Hardware Design Files
    KiCAD project + BoM for LCSC + Gerbers + P&P file + PDF Schematic + STEP 3D model
    [BoM.csv, CLN17-V1.kicad_pcb, CLN17-V1.kicad_sch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]
2023-10-27 V1.1 fixes
    - Optimised circuit power supply:
    - Improved power polygon layout;
    - Improved DCDC converter layout
    - Improved Type-C compatibility:
    - Added full-featured UCPD interface;
    - Added 5.1k resistors in case UCPD doesn't work
    - Optimised components:
    - ESD protection reduced form factor;
    - Correct USB Type-C connector with both CC lines
    [BoM.csv, CLN17-V1.kicad_pcb, CLN17-V1.kicad_sch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]
2023-12-20 Added block diagrams, schematics and .step files for V1.5 and V2.0
2023-12-29 Updated hardware design structure
    [BoM.csv, CLN17-V1.0.kicad_pcb, CLN17-V1.0.kicad_sch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]
2024-01-21 Released CLN17 V1.5 hardware design
    [CLN17-V1.5.kicad_sch, bom.csv, positions.csv]
2024-01-22 Minor documentation updates
    - added CLN17 V2 information
    - added board diagram for CLN17 V2
    - minor updates to README
    - added board requirements for V1.5
2024-01-27 A bit of firmware, a bit about hardware
    - Added a few notes about manufacturing v1.5 boards
    - Published pinout for V1.5 and V2.0
    - Added TLE5012B register library
    - Added test code for USB + HSE test
    - Other minor changes
2024-03-30 CLN17 V2 design improvements
    - Removed CAN-bus termination resistor [the termination resistor will be integrated into the wire to avoid mix-ups]
    - Changed current shunt rating from 20mR to 50mR, amplifier from 50V/V to 20V/V [noise reduction]
    - Removed fuse as the DRV8844 integrated OCP works good enough [optimise price and avoid potential problems]
    - Replaced LDO with a less noisy one, noise reduction improved from 50db@1kHz to 70db@1kHz [noise reduction]
    - Added ferrite to analogue supply [noise reduction]
    - Added pull-up to ground on PC13, PC14, PC15 [software version detection]
2024-03-31 CLN17 V1.5 design improvements
    - Added pull-up to ground on PC6, PC13, PC14, PC15 [software version detection]
    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
    [CLN17-V1.0.kicad_pcb, CLN17-V1.0.kicad_sch, CLN17-V1.5.kicad_sch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]
2024-06-30 CLN17 V2.0 source files released
    Release of the CLN17 V2.0 source files on the occasion of the completion of the Beta batch production.
    [CLN17-V2.0.kicad_pcb, CLN17-V2.0.kicad_sch, bom.csv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]
2024-07-03 Released enclosure design for CLN17 V1.5 and V2.0
    [BASE-ALUMINUM.STEP, COVER-ALUMINUM.STEP, COVER-POLYMER-TRANSPARENT.STEP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]
2025-12-09 Release of CLN17 V2.1 and CLN17 V2.5 design files, announce of CLN17 V3.0
    [CLN17-V1.5-3D.STEP, CLN17-V1.5.kicad_pcb, CLN17-V1.5.kicad_sch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]

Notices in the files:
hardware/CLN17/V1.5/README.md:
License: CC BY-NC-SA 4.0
